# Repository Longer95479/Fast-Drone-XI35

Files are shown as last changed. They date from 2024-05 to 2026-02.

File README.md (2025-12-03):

---
layout: post
title:  "XI35 装机全过程"
date:   2024-07-15 11:40:00 +0800
tags: quadcopter drone
categories:
    - fast-drone
---

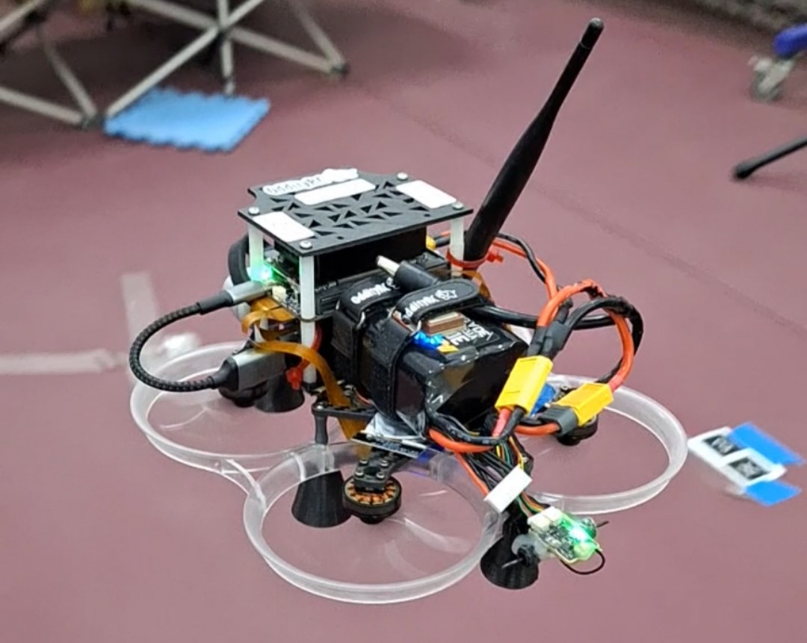
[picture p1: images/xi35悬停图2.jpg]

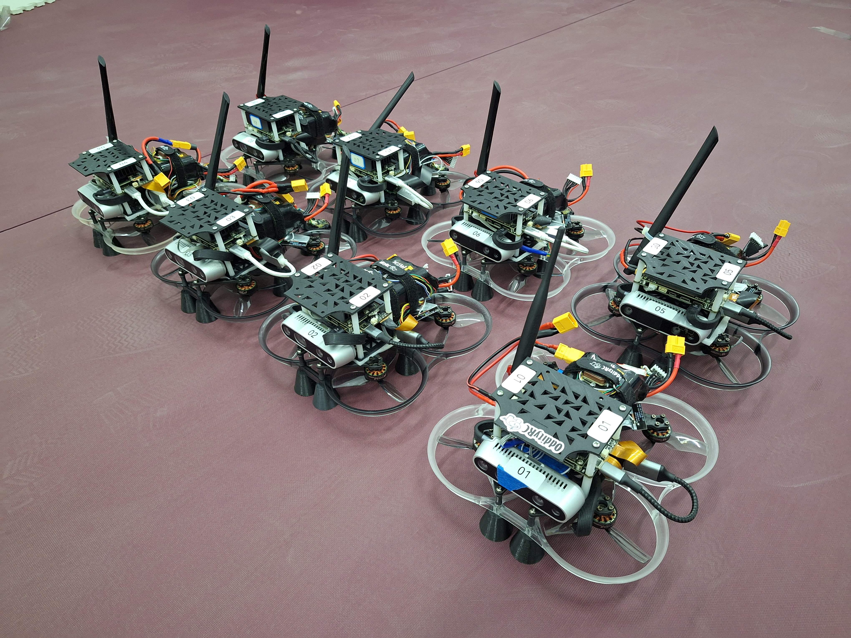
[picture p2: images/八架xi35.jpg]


本文介绍了：
- 152mm 轴距四旋翼无人机（XI35）的组装过程
- 飞控的参数配置
- 机载电脑 Jetson Orin 的系统安装与环境配置，有两种选择
  - 在宿主机上逐步地手动配置环境
  - 使用 Docker 自动配置环境
- 代码编译与启动流程
- [ ] TODO 开发流程
- 注意事项
- 开发流程

未包含的内容主要有：
- 各个模块的原理和设计逻辑
- 注意事项的具体分析

> 若需了解，可阅读本工程的其他文档，以及公开的论文。

本工程实现的功能：
- 在轴距更小的 XI35 上实现 fast-drone-250 的自主飞行避障功能
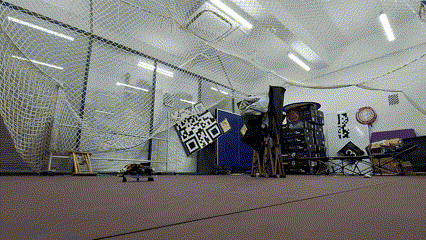
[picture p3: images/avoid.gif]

  
- 双机通信协同
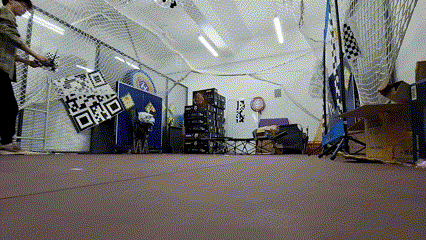
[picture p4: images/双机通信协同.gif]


- 预设航迹，搜索特定数字标识，正确识别后并降落
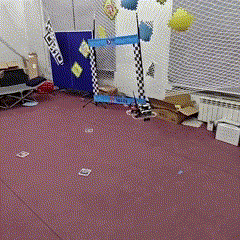
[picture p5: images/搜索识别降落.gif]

  
- 自主跟随墙面飞行
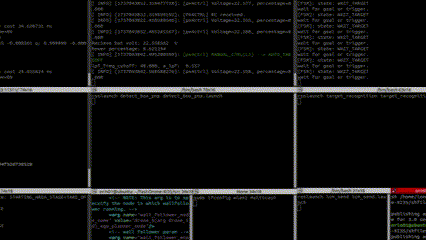
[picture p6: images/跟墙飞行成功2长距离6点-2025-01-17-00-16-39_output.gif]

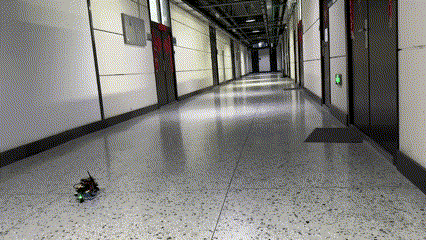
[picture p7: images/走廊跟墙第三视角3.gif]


## 目录
- [0 阅读指南](#0-阅读指南)
- [1 机体安装步骤](#1-机体安装步骤)
- [2 飞控配置](#2-飞控配置)
- [3 orin nx 配置](#3-orin-nx-配置)
- [4 docker 配置与使用](#4-docker-配置与使用)
- [5 代码编译与启动流程](#5-代码编译与启动流程)
- [6 开发流程](#6-开发流程)
- [注意事项](#注意事项)
- [参考](#参考)

## 0 阅读指南

当需要了解某个无人机部件的具体信息时：
- 所有的 `配件型号` 及 `配件的相关资料` 可在 [配件型号采购表](https://docs.qq.com/sheet/DQlVFVXBTYkpobktF?u=4ce3cf3cb1fc4960917789399c899a1a&tab=bliok2) 中找到。

从零开始组装到实现自主飞行避障：
- 可以先简单浏览第 0 - 5 章，以及 `注意事项` 和 `参考` 章节
- 简单浏览 Fast-Drone-250 的文本教程 和 视频教程
- 之后按 0-5 章的顺序安装和配置
- 遇到问题，可查看 `注意事项` 与 `参考` 章节是否提及，配合搜索引擎查找

在现有代码上开发：
- 阅读第 6 章开发流程

## 1 机体安装步骤

### 1.1 整体流程

- 将电机安装到机架上，使用四个M2*6，注意机架的上下面，孔位有凹槽的为上面

- 穿电池绑带

- 将M3转M2橡胶减震柱穿过电驱和飞控的四角安装孔（技巧：橡皮筋技巧）

- 使用M2*20安装电驱，8pin接口朝机头，接口贴着机架

- 电机线修修剪（用剥线钳），焊接(加松香)；电源线和滤波电容焊接

- 连接飞控（见下面QCG版本问题），连接电池，更改电机序号映射和转向

- 连接接收机（遥传一体模块中靠近LED的是RC接口）到飞控的 RC 端口，数传（遥传一体模块中的另一个接口）到 TELEM1 端口，GPS模块连接 到 GPS 端口

- 线穿过镂空部分把这几个模块都放到机架顶部

- ~~（略）M2\*12固定摄像头座，M2\*16固定图传天空端~~

- M3*6安装前六个铝柱的上部，<font color="#dd0000">第七个在尾部的立柱先不装</font>（b站视频说错了，应该看三维动图）

- ~~（略）M2\*12安装配重打印件~~

- 3d打印天线座安装，大的套在机架尾部，小的套在涵道圈，打印件有弹性，孔偏小，需要M3螺丝旋转	着才能穿过

- <font color="#dd0000">把各个数据线的飞控端都装上（tele2（连接到orin的），gps，接收机）</font>

- 机架，七个铝柱，涵道圈，菱形底架，从上至下叠起来后从下往上安装M3*14

- 调试完成后安装桨叶，使用M2*10安装

- 打印相机和orin的安装连接件，都是M2，立柱也是M2，配合螺母安装
    - orin载板安装孔是M3，使用M2立柱，导致只能用M2螺丝，螺帽太小会穿过，<font color="#dd0000">因此要在螺丝上加两个螺母</font>

- <font color="#dd0000">飞控上的 uart4（/dev/ttyS3） 连接到 ORIN 的 uart1（/dev/ttyTHS0）（左侧端口）</font>

参考：[NxtPX4v2开源飞控装机和配置全流程教程](https://www.bilibili.com/read/cv33197403/)

### 1.2 px4 与 orin 串口连接线的线序与焊接

由于 nxt-px4 和 orin 载板上的串口端口型号不同，需要将各自配套的线材剪断，并按照串口正确的线序进行焊接，线序对应关系如下：

|nxt-px4|黑(GND)|红(5V)|黄(Tx)|绿(Rx)|
|---|---|---|---|---|
|orin|3(GND)|x(5V)|1(Rx)|2(Tx)|

## 2 飞控配置

### 2.1 基本配置

- 测试电机转向

- 遥控器和接收机对频，并在地面站校准

- 配置通道功能，用于飞行模式切换、紧急停止等（注意：有三档的前两档一致）详见 [px4ctrl](https://gitee.com/jerry-ironman/px4ctrl)
  - 5通道2档：自稳和offboard
  - 6通道3档：是否接受命令
  - 7通道3档：急停
  - 8通道2档：px4ctrl对px4的重启

- 飞控与罗盘方向设置

- 陀螺仪与加速度计校准

- 校准地平线

细节参考 [NxtPX4v2开源飞控装机和配置全流程教程](https://www.bilibili.com/read/cv33197403/)

### 2.2 与 ORIN 通信相关的配置

主要参考 [Nxt-FC](https://github.com/HKUST-Aerial-Robotics/Nxt-FC?tab=readme-ov-file)，github 上的 readme 进行设置，<font color="#dd0000">不要按照商家给的安装教程里的进行设置</font>。主要是配置 MAV_0 的参数

- MAV_0_CONFIG: TELE2 (Serial Configuration for MAVLink (instance 0))
- MAV_0_FLOW_CTRL: Auto-detected
- MAV_0_FORWARD: Enabled
- MAV_0_MODE: External Vision
- MAV_0_RADIO_CTL: Enabled
- MAV_0_RATE: 921600 B/s

获得高分辨率和高频率的 IMU 数据所需的配置

create file in your tf-card /etc/extras.txt

```shell
mavlink stream -d /dev/ttyS3 -s ATTITUDE -r 200

mavlink stream -d /dev/ttyS3 -s HIGHRES_IMU -r 1000
```

then using the following settings:
- IMU_GYRO_RATEMAX: 2000Hz
- IMU_INTEG_RATE: 400Hz

after these settings you will have 250Hz /imu/data_raw /imu/data

## 3 ORIN NX 配置

### 3.1 安装 jetpack 5.1.3 linux for jetson orin nx modules:

- 在 PC 上的 ubuntu 里安装 sdkmanager

- 按住 REC 键并给 orin 上电，上电后可松开，之后将 typeC 插到 Recovery Port（在底板短边上的那个typec口，即 USB1），另一端连接到 PC

- 按照 sdkmanager 的引导操作即可，可选择组件安装
    - 此时 opencv 可以不装，因为此阶段安装的 opencv 不支持 cuda 加速

- 下载镜像

- 安装镜像
    - <font color="#dd0000"> 注意 username不能是大写字母，否则 sdkmanager 无法自动设置orin的用户名等后续的默认设置参数，进一步导致无法通过usb以太网连接orin </font>

    - <font color="#dd0000"> 一切安装完成后，忘记拔掉 usb 将导致板子一直无法正常启动，外接屏幕无画面，拔掉后就一切正常 </font>

- 如果 PC 上的 ubuntu 硬盘空间不足，可外接移动硬盘，将 Download Folder 和 Target HW image folder 设置在移动硬盘（FAT）里
    - <font color="#dd0000"> 注意：移动硬盘的文件系统不能是 windows 的 FAT，而应该是 EXT4，否则镜像将会安装错误 </font>

### 3.2 ROS 安装

参考 [从零制作自主空中机器人](https://github.com/ZJU-FAST-Lab/Fast-Drone-250/tree/master):

* `sudo sh -c 'echo "deb http://packages.ros.org/ros/ubuntu $(lsb_release -sc) main" > /etc/apt/sources.list.d/ros-latest.list'`

* `sudo apt-key adv --keyserver 'hkp://keyserver.ubuntu.com:80' --recv-key C1CF6E31E6BADE8868B172B4F42ED6FBAB17C654`

* `sudo apt update`

* `sudo apt install ros-noetic-desktop-full`

* `echo "source /opt/ros/noetic/setup.bash" >> ~/.bashrc`

* <font color="#dd0000">建议没有ROS基础的同学先去B站学习古月老师的ROS入门教程</font>

测试 ROS:
* 打开三个终端，分别输入
  * `roscore`
  * `rosrun turtlesim turtlesim_node`
  * `rosrun turtlesim turtle_teleop_key`

### 3.3 realsense 驱动安装

* `sudo apt-key adv --keyserver keyserver.ubuntu.com --recv-key  F6E65AC044F831AC80A06380C8B3A55A6F3EFCDE || sudo apt-key adv --keyserver hkp://keyserver.ubuntu.com:80 --recv-key  F6E65AC044F831AC80A06380C8B3A55A6F3EFCDE`

* `sudo add-apt-repository "deb https://librealsense.intel.com/Debian/apt-repo $(lsb_release -cs) main" -u`

* `sudo apt-get install librealsense2-dkms`

* `sudo apt-get install librealsense2-utils`

* `sudo apt-get install librealsense2-dev`

* `sudo apt-get install librealsense2-dbg`

* 测试：`realsense-viewer`

* <font color="#dd0000">注意测试时左上角显示的USB必须是3.x，如果是2.x，可能是USB线是2.0的，或者插在了2.0的USB口上（3.0的线和口都是蓝色的）</font>

- <font color="#dd0000">roslaunch realsense2_camera rs_camera.launch 无法正常工作，报符号错误，这是是手使用动编译的opencv4.5.4但没添加对应路径的问题 </font>
    - 解决参考 [librealsense2 camera.so: undefined symbol:ZN2cV3MatC1EV 解决笔记记录](https://blog.csdn.net/weixin_46151178/article/details/129729719)

### 3.4 安装 mavros

* `sudo apt-get install ros-noetic-mavros`
* `cd /opt/ros/noetic/lib/mavros`
* `sudo ./install_geographiclib_datasets.sh`
*  `roscd mavros`，修改 px4.launch 的串口波特率（921600）和串口名字（ttyTHS0）

### 3.5 安装ceres与glog与ddyanmic-reconfigure

* 解压`3rd_party.zip`压缩包

* 进入glog文件夹打开终端

* `sudo chmod 777 autogen.sh && sudo chmod 777 configure`

* `./autogen.sh && ./configure && make && sudo make install`

* `sudo apt-get install liblapack-dev libsuitesparse-dev libcxsparse3.1.2 libgflags-dev libgoogle-glog-dev libgtest-dev`

* 进入ceres文件夹打开终端

* `mkdir build`

* `cd build`

* `cmake ..`

* `sudo make -j4`

* `sudo make install`

* `sudo apt-get install ros-noetic-ddynamic-reconfigure`

<font color="#dd0000"> 注意，安装的版本是 `ceres 2.0.0` 版本，编译需使用 `std=c++14` 及以上，后续需把 vinsfusiongpu 里的所有包都改成 c++14 标准 </font>

### 3.6 OpenCV 安装

如果我们在 sdkmanager 中勾选了安装 opencv 的选项，安装的版本将会是 `OpenCV 4.5.4`，但不支持 cuda 加速，此时我们下载相同版本的 opencv 源码，在 CMAKE 选项上打开支持 cuda 加速的选项，再进行编译。

安装过程参考 [Jetson Orin NX 开发指南（5）: 安装 OpenCV 4.6.0 并配置 CUDA 以支持 GPU 加速](https://blog.csdn.net/qq_44998513/article/details/133778446)，注意版本的不同即可，我们安装的是 4.5.4
* install 的目录为 /usr/local/opencv-4.5.4，方便其他包的查找

<font color="#dd0000">注意，编译支持cuda的 opencv时，cmake选项里 CUDA_ARCH_BIN=8.7，而不是 7.2 </font>

### 3.7 安装 cv_bridge 功能包

为什么需要自己下载 cv_bridge 源码并编译呢？

安装 noetic full版本时已经下载了 cv_bridge 的二进制文件，其编译时使用的是 opencv 4.2 的函数，因此链接时需要链接到opencv 4.2的 so 文件，但 orin 上新安装的支持 cuda 加速的 opencv 是 4.5.4 版本，因此该 cv_bridge 只能链接到 4.5 版本的 opencv 库，vins 在执行到 cv_bridge 相关的函数时就无法正常执行，最后报内存溢出的错。

解决办法：下载 cv_bridge 的源码，然后指定 4.5 版本的opencv进行编译，编译完成后将其路径添加到 ~/.bashrc 文件中，并刷新环境变量，具体参考 [Jetson Orin NX 开发指南（5）: 安装 OpenCV 4.6.0 并配置 CUDA 以支持 GPU 加速](https://blog.csdn.net/qq_44998513/article/details/133778446)

或者是将 cv_bridge_454 的包放入同一个工作空间，其他包在 CMakeList.txt 和 package.xml 里指明依赖，一同编译即可，这是目前的做法

### 3.8 下载并编译 Fast-drone-XI35

原本需要分成两部：

- clone 浙大官方的 Fast-drone-250 的仓库
- 将其中的 vins-fusion 替换成 fins-fusion-gpu 版本

为了简化操作：
- [x] 把替换成 gpu 版本的 fast-drone-250 push 到 [Fast-Drone-XI35](https://github.com/Longer95479/Fast-Drone-XI35)，**直接 clone 该仓库即可，之后进行编译**。

其中所作的修改均是针对的 vins-fusion-gpu，包括：

- 由于 ceres 2.0.0 需使用 std=c++14，因此把 vinsfusiongpu 里的所有包的 CMakeLists.txt 都改成 c++14 标准

- 设置 OpenCV 路径为带有 GPU 加速的 opencv 4.5.4，opencv 可以指定到 `编译的文件夹` 或 `安装的文件夹`

- 由于 vins-fusion-gpu 原仓库使用的是 opencv 3，而现在安装的是 opencv 4，OpenCV 4 系列和 OpenCV 3 系列有一些变量的名称发生了改变，因此我们这里只要将相应的变量名称进行修正，就能顺利通过编译

- 具体参考：[Jetson Orin NX 开发指南（6）: VINS-Fusion-gpu 的编译和运行](https://blog.csdn.net/qq_44998513/article/details/133780129)

### 3.9 网络配置

- 使用 `iw list` 查询网卡是否支持Ad-Hoc模式，如果Supported interface modes中出现IBSS，则说明网卡支持Ad-Hoc模式

- 使用 `ifconfig` 查询想要配置成Ad-Hoc模式网卡的名称

- 使用Network Manager配置网卡，ifname为待配置的网卡名称，con-name为配置文件名称，ssid为网络名称，wifi.band为频段，wifi.channel为信道
```shell
sudo nmcli connection add type wifi ifname wlan1 con-name HITADHOC mode adhoc ssid HITADHOC wifi.band bg wifi.channel 3
```

- 通过con-name修改网络配置，ipv4.addresses为IPv4地址
```shell
sudo nmcli connection modify HITADHOC ipv4.method manual ipv4.addresses 10.10.10.11/24
```

- 通过con-name激活网络配置，激活后会开机自启动
```shell
sudo nmcli connection up HITADHOC
```

- 如果后续要删除配置，可以通过con-name删除
```shell
sudo nmcli connection delete HITADHOC
```

- LCM 安装
```shell
git clone https://github.com/lcm-proj/lcm && \
cd lcm && \
git checkout tags/v1.4.0 && \
mkdir build && cd build && \
cmake -DCMAKE_BUILD_TYPE=Release -DBUILD_TESTING=OFF -DBUILD_EXAMPLES=OFF -DBUILD_BENCHMARKS=OFF .. && \
make -j${USE_PROC} && make install
```

- LCM通信配置
```shell
sudo ifconfig wlan1 multicast
sudo route add -net 224.0.0.0 netmask 240.0.0.0 dev wlan1
```

### 3.10 安装 onnxruntime

```shell
pip install onnxruntime
```

### 3.11 安装 skimage
```shell
pip install scikit-image
```

## 4 Docker 配置与使用
底层基础镜像：NVIDIA L4T JetPack r35.3.1
官方镜像地址：https://catalog.ngc.nvidia.com/orgs/nvidia/containers/l4t-jetpack
### 4.1 构建基础环境镜像Dockerfile.jetson_base
基础环境镜像包含了运行Fast-Drone-XI35所需要的各种软件库。
- ros-noetic-base及其部分功能包
- OpenCV4.5.4-cuda版本
- cv_bridge4.5.4，适配的opencv4.5.4，已添加进ros环境，功能包名称cv_bridge_454
- realsense2驱动库
- mavros功能包
- glog-0.5
- ceres-2.0.0
- lcm

部分软件库（ceres、glog和cv_bridge）和编译一些软件库所需要的额外的文件（比如编译opencv_contrib需要一些额外文件）打包进一个压缩包3rd_party.zip，放在docker执行的上下文目录，供构建镜像时解压使用。
构建环境基础镜像，在终端执行：
```shell
make jetson_base
```

**具体使用见 4.6**

### 4.2 构建Fast-Drone-XI35工程镜像Dockerfile.jetson
在Dockerfile.jetson_base的基础上构建，从github上拉取最新的Fast-Drone-XI35并进行编译，加入容器初始化脚本。
由于dockerhub在国内无法访问，基础环境镜像暂时没有push到远程仓库，通过docker save打包成.tar文件，借助u盘拷贝至宿主机，再通过docker load解压得到基础环境镜像local/fastdronexi35:orin_base_35.3.1。
要构建Fast-Drone-XI35镜像，在终端执行:
```shell
make jetson
```
初始化脚本"container_init.sh"说明：
初始化脚本也放在构建镜像的上下文目录，构建阶段拷贝至镜像/root目录下，用于执行启动容器时的一些初始化操作，目前的初始化操作比较简单，主要是启动ssh服务，还有一个操作是改变mavros的px4.launch中的参数用于设配实际硬件，这样避免了重新构建基础镜像。
### 4.3 容器启动脚本说明
容器启动脚本“container_run.sh”用于对Fast-Drone-XI35工程镜像执行docker run操作，并实现必要的自定义配置，后续可根据需求进行修改，下面对目前容器启动配置进行详细介绍。
```shell
docker run -itd --privileged=true --network host \
        --mount type=bind,source=${HOME}/Docker_Data,target=/root/data \
        --mount type=bind,source=/dev,target=/dev \
        --mount source=Fast-Drone-XI35,target=/root/Fast-Drone-XI35 \
        --runtime=nvidia --gpus all \
        --name fd_runtime \
        fastdronexi35:orin /bin/bash
```
- 通过“--privileged=true”赋予容器对宿主机全面的访问权限，再通过“--mount type=bind,source=/dev,target=/dev”挂载宿主机的/dev实现容器对宿主机设备资源的无障碍访问。
- “--network host”配置容器的网络模式为host主机模式，容器和宿主机共享ip和端口号，相比于需要进行端口映射bridge模式，host模式下更方便远程主机与容器实现双向通信，比如ros多机的场景。但要注意与宿主机端口冲突的问题。
- “--mount type=bind,source=${HOME}/Docker_Data,target=/root/data”通过bind mounts将宿主机指定目录挂载至容器内。宿主机目录需要提前建立，并且宿主机目录不管是否为空都会覆盖容器目录（相当于在容器内创建了指向宿主机目录的软连接），主要用于共享宿主机数据以及永久性存储容器的数据。
- “--mount source=Fast-Drone-XI35,target=/root/Fast-Drone-XI35”通过数据卷（volumes）挂载方式，实现Fast-Drone-XI35工程目录在宿主机和容器之间的双向互通，此操作会在宿主机docker目录下创建数据卷，并在启动容器时将容器内的Fast-Drone-XI35挂载到数据卷，类似于软连接，在数据卷中的修改会同步到容器，从而便于在宿主机直接修改代码。注意启动容器时若数据卷不为空，则数据卷会覆盖容器目录。
- “--runtime=nvidia  --gpus all”使容器能访问gpu，前提是已经装好NVIDIA Container Toolkit，官方安装教程：https://docs.nvidia.com/datacenter/cloud-native/container-toolkit/latest/install-guide.html
### 4.4 VSCode SSH配置
通过vscode的Remote SSH插件远程连接至宿主机，在资源管理器打开挂载Fast-Drone-XI的数据卷，即可实现代码开发（前提是容器内Fast-Drone-XI正确挂载到宿主机数据卷）。实现步骤如下：
- 安装remote-ssh插件

<p align="center">
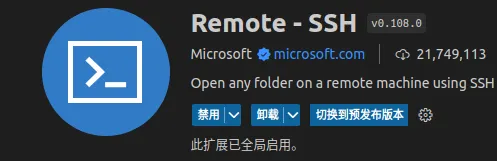
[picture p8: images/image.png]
  
</p>

- 点击左侧的远程资源管理器，点击“+”新建远程，输入宿主机的用户名和ip，由于访问docker的数据卷需要root权限，所以需要以root身份登录，即用户名为root。

<p align="center">
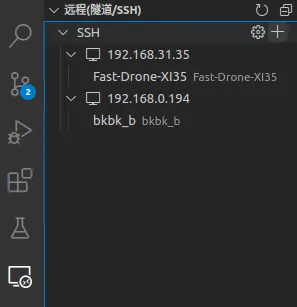
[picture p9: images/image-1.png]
  
</p>

如果无法登录，检查宿主机的root密码是否正确，一般情况下ubuntu的root没有初始密码，这种情况下无法以root登录的，需要通过“sudo passwd root”重新设置root密码。

- 登录成功后即可编辑代码，并且修改会同步至容器。

<p align="center">
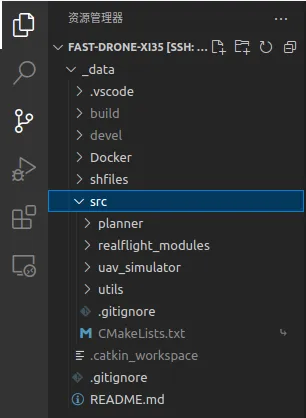
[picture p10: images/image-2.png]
  
</p>

### 4.5 Fast-Drone-XI35远程同步更新
需求场景：github远程仓库有更新，需要更新容器内的Fast-Drone-XI35。
目前有两种更新方式，宿主机更新和工程镜像更新。
- 宿主机更新：
容器内Fast-Drone-XI35已挂载到宿主机的docker数据卷，对数据卷的任何操作都会同步到容器内，因此可以对宿主机的Fast-Drone-XI35数据卷使用git pull更新工程。这种更新方式效率高，但是更新发生在宿主机数据卷，没有更新镜像，若要形成新的镜像，需要对容器进行commit。
- 工程镜像更新：
重新构建工程镜像，构建时会拉取远程仓库最新的版本，最后生成带有Fast-Drone-XI35最新版本的镜像。主要流程如下：
①停止并删除正在运行的容器（fd_runtime）
②删除工程镜像（fastdronexi35:orin）
③删除宿主机Fast-Drone-XI35数据卷
④运行make jetson构建新的工程镜像
上述操作已集成在"update_jetson.sh"脚本中，当需要进行镜像更新时，直接运行该脚本即可，注意需要宿主机有基础环境镜像（tag为"local/fastdronexi35:orin_base_35.3.1"），否则无法构建。
### 4.6 容器部署简要流程

首先 clone 本仓库，之后的从构建基础环境镜像到运行容器的整个流程，所有命令在/Docker/Dockerfile目录下执行。

```shell
git clone https://github.com/Longer95479/Fast-Drone-XI35.git
```

- 构建基础环境镜像: local/fastdronexi35:orin_base_35.3.1
```shell
make jetson_base
docker tag fastdronexi35:orin_base_35.3.1 local/fastdronexi35:orin_base_35.3.1
```
或者 直接从移动硬盘里加载镜像的 tar 文件
```shell
sudo docker load -i fastdronexi35_base.tar
```

- 在本工程的 `/Docker/Dockerfile`下执行命令，构建工程镜像: fastdronexi35:orin
```shell
make jetson
```
- 首次编译完成后，执行容器启动脚本
```shell
./container_run.sh
```

后续重启后，只需执行以下命令启动容器
```shell
sudo docker start fd_runtime
```

- 进入容器的 bash

```shell
sudo docker exec -it  fd_runtime bash
```

- 如果需要更新工程镜像，则执行
```shell
./update_jetson.sh
```

## 5 代码编译与启动流程

### 5.1 前置准备

**1.使用网卡局域网连接无人机**

配置网卡
- 使用Network Manager配置网卡，ifname为待配置的网卡名称，con-name为配置文件名称，ssid为网络名称，wifi.band为频段，wifi.channel为信道(只需更改wlan1为无线网卡)

  ```sudo nmcli connection add type wifi ifname wlan1 con-name HITADHOC mode adhoc ssid HITADHOC wifi.band bg wifi.channel 3```

- 通过con-name修改网络配置，ipv4.addresses为IPv4地址(10.10.10.11中末位的11-19是无人机用的ip，不要重复设置)

  ```sudo nmcli connection modify HITADHOC ipv4.method manual ipv4.addresses 10.10.10.11/24```

- 通过con-name激活网络配置，激活后会开机自启动

  ```sudo nmcli connection up HITADHOC```

- 如果后续要删除配置，可以通过con-name删除

  ```sudo nmcli connection delete HITADHOC```

- 查看已配置的网络连接

  ```sudo nmcli con show```

- 连接无人机

  ```ssh orin04@10.10.10.14```

**2.获取ip地址后使用路由器连接**

- 使用nmcli命令配置wifi连接

  ```sudo nmcli device wifi```

- 查询wifi列表

  ```sudo nmcli device wifi list```

- 更改连接wifi(查找不到wifi时重新扫描)

  ```sudo nmcli device wifi connect Drone_WiFi password buzhidao```

- 查看ip

  ```ifconfig```

- 使用局域网连接

  ```sh orin04@192.168.3.101```

**3.使用terminator连接**

- 查看隐藏文件和文件夹

  ```ls -a```

- 查找terminator配置文件(.config/terminator目录下)

  ```cd ~/.config/terminator```

- 查看当前目录下文件的详细信息，terminator中仅有config文件发挥作用，所以重只需查看config的软路由

  ```ll```

- 默认使用网卡连接，如果需要更改为wifi连接，可以替换原有配置中的本地ip后更改路由

- vim 内的批量替换命令

  ```:%s/10.10.10.11/192.168.3.100/g```

- 更改软路由

  ```sudo ln -sf config-orin01-nodocker config```

- 打开无人机控制系统

  ```terminator -l drone_1```

### 5.2 运行无人机的不同功能

- ssh 连接到 orin 板，如 `ssh orin01@10.10.10.11`

悬停功能：

- 启动里程计
  - `sh Fast-Drone-XI35/shfiles/rspx4.sh`

- 启动运动控制器
  - `roslaunch px4ctrl run_ctrl.launch`

可选功能：

- 启动 ego-planner
  - `roslaunch ego_planner single_run_in_exp.launch`

- 打开下视摄像头，并进行数字标识检测、定位、识别
  - `roslaunch jetson_csi_cam jetson_csi_cam.launch sensor_id:=0`
  - `roslaunch detect_box_pnp detect_box_pnp.launch`
  -  `roslaunch target_recognition target_recognition.launch`

- 打开多机协同搜索的状态机，以及目标结果融合
  - `roslaunch search_plan search_plan.launch`
  - `roslaunch target_merge target_merge.launch`

- 打开多机自组网通信
    - `sudo ifconfig wlan1 multicast`
    - `sudo route add -net 224.0.0.0 netmask 240.0.0.0 dev wlan1`
    - `roslaunch lcm_receive lcm_receive.launch`
    - `roslaunch lcm_send lcm_send.launch`

起飞：

- `sh Fast-Drone-XI35/shfiles/takeoff.sh`

### 5.3 调参

一些常用的参数可能需要频繁调整，但参数分布在不同文件里，为了提高修改效率，编写了脚本批量修改参数，无需直接在原文件内修改，只需在 `Fast-Drone-XI35/config_scipt` 目录下修改 `xxx.yaml` 配置文件，文件里已列出一系列参数和值。修改完毕后可执行脚本 读取 和 真正写入 参数：

```
python3 read_global_config.py global_config_indoor.yaml
python3 set_global_config.py global_config_indoor.yaml
```

如需了解有哪些参数需要配置，请阅读 `config_scipt/global_config_indoor.yaml` 文件。大致可分为两类：
- 机间特异性配置
- 与飞行场地大小相关的参数配置

pid 的参数需单独在 `Fast-Drone-XI35/src/realflight_modules/px4ctrl/config` 文件内修改。

## 6 开发流程
### 曲线日志的使用与解析
在开发过程中，难免有时需要对一个变量随时间的变化情况进行观察，或者对自己打印的某个log在实验结束后进行复盘，基于此开发了如下功能：

- 将ROS自带的文件系统日志记录到代码主目录下的/log文件夹

- 通过在代码中调用ROS日志输出特定格式的键值对来记录“曲线日志”

- 使用/scripts/process_log.py对所有架次的日志进行解析，输出为文本日志和csv曲线日志

下面是具体开发指南：

1. 修改ROS日志在文件系统内的默认位置

ROS的日志在启动时会获取ROS_LOG_DIR环境变量的值，将日志保存在此位置，所以需要在.bashrc添加一个环境变量。

- 在非Docker环境中，需要在~/.bashrc中自行添加环境变量（下面的绝对路径换成自己的代码中log目录位置）。

```
export ROS_LOG_DIR=/home/zhangrun/code/Fast-Drone-XI35/log
```

- 在Docker环境中，配置脚本已经添加了加入环境变量的步骤，所以无需操作。

2. 在代码中记录曲线日志

通过键值对[status]:[12.76]的格式调用ROS_INFO或ROS_WARN或ROS_INFO_THROTTLE等进行记录，如：

```
ROS_INFO("[odom_tx]:[%f] [odom_ty]:[%f] [odom_tz]:[%f], tmp_T.x(), tmp_T.y(), tmp_T.z());
```

注意只支持英文字母。

3. 日志解析

通过在代码/scripts/process_log.py脚本进行解析处理

```
python3 scripts/process_log.py
```

将会有如下输出：

```
Processing /home/zhangrun/code/Fast-Drone-XI35/scripts/../log/2d61da22-a4b5-11f0-b4af-488f4b616bfc ...
Done: /home/zhangrun/code/Fast-Drone-XI35/scripts/../log/2025-10-09 10:10:50
Processing /home/zhangrun/code/Fast-Drone-XI35/scripts/../log/711678c8-a4b4-11f0-9342-488f4b616bfc ...
Done: /home/zhangrun/code/Fast-Drone-XI35/scripts/../log/2025-10-09 10:05:34
```

上边参考输出表示将2d61da22-a4b5-11f0-b4af-488f4b616bfc文件夹的日志输出到log/2025-10-09 10:10:50目录下，其中有两种日志：'2025-10-09 10:10:50.csv'  '2025-10-09 10:10:50.log'，分别对应曲线日志和文本日志。

4. 曲线日志的查看

通过ROS的Plotjuggler进行查看.csv格式的曲线日志。亦可以将日志下载到Windows电脑，通过win平台的Plotjuggler进行查看

安装：

```
sudo apt install ros-noetic-plotjuggler-ros
```

启动：
```
rosrun plotjuggler plotjuggler
```

导入.csv文件，选定timestamp为X轴后，将想要显示的曲线拖动到右侧表中即可显示。

<p align="center">
  <img src="images/plotjuggler-1.png" width="90%">
</p>

<p align="center">
  <img src="images/plotjuggler-2.png" width="90%">
</p>

## 注意事项

### 飞控相关

- 安装好后typeC不好插

- 小心滤波电容短路

- QGC v4.0.11无法识别 px4 pro 1.14.0
  - QGC 4.3.0 可以识别

- imu频率在地面站上看一直是50Hz，不知用NX板连接 SER_TELE2 时会不会达到250Hz
  - 会

- 智能充充电电流设置为1.3A会时不时自动停止充电，需要频繁人为重启，设置为1A则正常（电池充放电能力为0.5C，既 3000mAh*0.5h^-1 = 1500mA = 1.5A）

- 电机线焊接方向没选择好，导致挤在一起，可能会影响散热
  - ！！！加上电源线没焊好，会挡住飞控上的 TELE2 接口，不得不重新焊接

### Orin 相关

- orin载板安装孔是M3，使用M2立柱，导致只能用M2螺丝，螺帽太小会穿过，因此要在螺丝上加两个螺母

- orin和nxtpx4通过串口相连，但两端的接口不同，需要自己焊接线

- px4的/dev/ttyS3 连接到 orin 的 /dev/ttyTHS0

- 安装ceres与glog与ddyanmic-reconfigure时，执行 ./autogen.sh && ./configure && make && sudo make install 前要加两句 sudo chmod 777 autogen.sh && sudo chmod 777 configure

- unable to locate package libcxsparse3.1.2
    - 使用sdkmanager预装的opencv不支持cuda，需要卸载，重新安装支持cuda加速的版本
    - 或者不卸载，直接安装支持 cuda 加速的版本，之后cmake文件里把路径指向编译所在的文件夹，因为卸载时用 autoremove会把 ros的full版本删掉一部分，需要重新下回来，并照着vinsfusiongpu的readme修改路径
    - 更好的操作是不要使用 sudo make uninstall 卸载 opencv，而是
        - 找到之前装opencv的build文件夹，进入后执行卸载指令 `sudo make uninstall`
        - 然后再把之前留在usr文件夹里的剩余文件都删掉
        - `sudo rm -r /usr/local/include/opencv4  /usr/local/share/opencv4 /usr/local/lib/libopencv* `
        - `sudo rm -r /usr/include/opencv4  /usr/share/opencv4 /usr/lib/libopencv* `
`

- roslaunch realsense2_camera rs_camera.launch 无法正常工作，报符号错误，这是是手使用动编译的opencv4.5.4但没添加对应路径的问题
    - 解决参考 [librealsense2 camera.so: undefined symbol:ZN2cV3MatC1EV 解决笔记记录](https://blog.csdn.net/weixin_46151178/article/details/129729719)

- VINS无法正常运行，原因有多个
  - 一个是是编译支持cuda的 opencv时， cmake选项里 CUDA_ARCH_BIN=8.7，填成了7.2
  - 另一个重要原因是，安装 noetic full版本时已经下载了 cv_bridge 的二进制文件，其编译时使用的是 opencv 4.2的函数，因此链接时需要链接到opencv 4.2的 so文件，但orin上新安装的支持cuda加速的opencv是 4.5.4 版本，因此该cv_bridge 只能链接到 4.5 版本的opencv库，vins在执行到cv_bridge 相关的函数时就无法正常执行，最后报内存溢出的错。解决办法：下载 cv_bridge 的源码，然后指定 4.5版本的opencv进行编译，编译完成后将其路径添加到 ~/.bashrc 文件中，并刷新环境变量
  - 参考 [Jetson Orin NX 开发指南（6）: VINS-Fusion-gpu 的编译和运行_jetson orin nx跑vins-CSDN博客](https://blog.csdn.net/qq_44998513/article/details/133780129)

- 设置好外参初始值后，里程计输出出现姿态较准确，但平移量反复波折，仿佛被约束在一点，不随实际运动而运动，且容易出现巨大漂移
  - 外参中旋转矩阵的符号错了，本来以为相机坐标系是z朝前y朝上，实际情况时z朝前y朝下，修改后里程计正常

- 自动起飞后会超调一下

- 飞行过程上下起伏，可能需要调一下PID参数

- 起飞和飞行时机身倾斜，需要校准一下地平线

- LCM节点启动后报错：Error while loading shared libraries: liblcm.so.1: cannot open shared object file: No such file or directory
    - [$ sudo ldconfig -v](https://github.com/CogChameleon/ChromaTag/issues/2)

### 调试相关

- 需要先生成公钥，然后执行该命令，之后便不需要再输入密码即可连接

  ```ssh-copy-id orin01@10.10.10.11```

- 命令行连接wifi

```shell
sudo nmcli device wifi list
sudo nmcli device wifi connect Drone_WiFi password buzhidao
```

- vim 内的批量替换命令

  ```%s/10.10.10.11/192.168.3.100/g```

- 更改软路由

  ```sudo ln -sf config-orin01-nodocker config```

- 常用参数修改，如起飞高度

```shell
/home/orin01/Fast-Drone-XI35/config_scipt
python3 read_global_config.py global_config_indoor.yaml
python3 set_global_config.py global_config_indoor.yaml
```

- pid调参

  ```/home/orin01/Fast-Drone-XI35/src/realflight_modules/px4ctrl/config```

- 打开无人机控制系统

  ```terminator -l drone_1```

## 参考

- [OddityRC XI35pro Assembly Guide](https://oddityrc.com/blogs/assembly-guides/xi35pro-frame-assembly-guide)

- [OmniNxt](https://hkust-aerial-robotics.github.io/OmniNxt/)

- [怪象XI35装机视频_哔哩哔哩_bilibili](https://www.bilibili.com/video/BV1Au411t7tV/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)

- [3.5寸圈圈机怪象XI35装机教程_哔哩哔哩_bilibili](https://www.bilibili.com/video/BV1QG411E7NQ/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)

- [NxtPX4v2开源飞控装机和配置全流程教程](https://www.bilibili.com/read/cv33197403/)

- [Jetson Orin NX 开发指南（5）: 安装 OpenCV 4.6.0 并配置 CUDA 以支持 GPU 加速](https://blog.csdn.net/qq_44998513/article/details/133778446)

- [Jetson Orin NX 开发指南（6）: VINS-Fusion-gpu 的编译和运行_jetson orin nx跑vins-CSDN博客](https://blog.csdn.net/qq_44998513/article/details/133780129)

- [Fast-Drone-250](https://github.com/ZJU-FAST-Lab/Fast-Drone-250)

- [wall-follower-fastdrone-250](https://github.com/Longer95479/wall-follower-fastdrone-250/)

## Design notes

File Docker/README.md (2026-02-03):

# Docker 使用

## nvidia jetson平台

1. 构建基础镜像

```bash
make jetson_base
```

2. 构建工程镜像

```bash
make jetson
```

3. 容器启动

```bash
### 首次容器启动
./container_run.sh
### 后续容器启动
docker start fd_runtime
docker exec -it  fd_runtime bash
```

## x86 平台

⚠️ 前置要求

1. 宿主机必须正确安装好Nvidia驱动，使用nvidia-smi测试输出，CUDA Version字段必须大于等于11.8

2. 宿主机必须正确安装好Nvidia Docker Toolkit
```bash
curl -fsSL https://nvidia.github.io/libnvidia-container/gpgkey | sudo gpg --dearmor -o /usr/share/keyrings/nvidia-container-toolkit-keyring.gpg \
  && curl -s -L https://nvidia.github.io/libnvidia-container/stable/deb/nvidia-container-toolkit.list | \
    sed 's#deb https://#deb [signed-by=/usr/share/keyrings/nvidia-container-toolkit-keyring.gpg] https://#g' | \
    sudo tee /etc/apt/sources.list.d/nvidia-container-toolkit.list

sudo apt-get update
sudo apt-get install -y nvidia-container-toolkit
sudo nvidia-ctk runtime configure --runtime=docker
sudo systemctl restart docker
```

3. 确认电脑的CUDA_ARCH_BIN，对Dockerfile.pc的ARG CUDA_ARCH_BIN=7.5（默认）进行修改

```bash
git clone https://github.com/NVIDIA-AI-IOT/deepstream_tlt_apps.git
cd deepstream_tlt_apps/TRT-OSS/x86
nvcc deviceQuery.cpp -o deviceQuery
./deviceQuery
### 输出
Detected 1 CUDA Capable device(s)

Device 0: "NVIDIA GeForce GTX 1660 SUPER"
  CUDA Driver Version / Runtime Version          12.2 / 11.8
  CUDA Capability Major/Minor version number:    7.5

CUDA Capability Major/Minor version number这个字段的数字就是CUDA_ARCH_BIN
###
```

4. 由于需要从docker Hub pull一个base镜像，需要提前解决docker的代理问题，否则会出错

参考：

```bash
vim /etc/docker/daemon.json
###
# 添加以下内容
{
 "registry-mirrors": ["https://docker.1ms.run", "https://docker.1panel.live/"]
}
###
sudo systemctl daemon-reload
sudo systemctl restart docker
```

1. 下载TensorRT到Docker文件夹下

下载地址（需要登录）：
https://developer.nvidia.com/downloads/compute/machine-learning/tensorrt/secure/8.6.1/tars/TensorRT-8.6.1.6.Linux.x86_64-gnu.cuda-11.8.tar.gz

2. 构建Docker镜像

```bash
cd Docker/Dockerfile
make pc
```

中间会提示

- ⚠️ Please download TensorRT and put it in the parent directory (../) url:https://developer.nvidia.com/downloads/compute/machine-learning/tensorrt/secure/8.6.1/tars/TensorRT-8.6.1.6.Linux.x86_64-gnu.cuda-11.8.tar.gz
Press any key to continue...
安装第一步下载好tensorRT文件到指定位置，此处可按任意键跳过

- Do you want to use a proxy? [y/n]
是否使用代理进行接下来的构建，由于github、国外软件源的存在，不使用代理会有几率存在网络问题，推荐使用代理，回车默认y

- Use default proxy (http://127.0.0.1:7897) (http://127.0.0.1:7897)?
默认代理地址指向本机代理软件的地址和端口，如果想要更改代理地址，输入n后进行修改。 ⚠️ 注意修改代理地址时，一般HTTP_PROXY和HTTPS_PROXY都是http开头的代理地址

构建完成后

```bash
docker image ls
```

输出

```bash
REPOSITORY      TAG IMAGE ID        CREATED         SIZE
fastdronexi35   pc  a615436b212d    19 hours ago    24.4GB
```

3. 实例化Docker容器

其中$TARGET_DIR需要替换为宿主机的代码目录，或者其他的想要映射到容器内的目录

- -v $TARGET_DIR:/root/Fast-Drone-XI35 作用是将宿主机的$TARGET_DIR目录映射到容器内的/root/Fast-Drone-XI35，实现宿主机和容器共同使用同一份文件。两个系统均可对文件进行修改。

```bash
xhost +local:root # 允许本地 root 显示 X 窗口

docker run -it \
--name fd_runtime_pc \
--gpus all \
--net=host \
--privileged \
-e DISPLAY=$DISPLAY \
-e QT_X11_NO_MITSHM=1 \
-v /tmp/.X11-unix:/tmp/.X11-unix:rw \
-v $TARGET_DIR:/root/Fast-Drone-XI35 \
fastdronexi35:pc \
bash
```

4. 测试容器

- 进入容器终端

```bash
docker exec -it fd_runtime_pc bash
```

- 建议将代码source setup.bash放入.bashrc环境变量中,同时配置ROS_LOG_DIR的环境变量，根据自己实际的容器中代码路径下述命令

```bash
echo 'export ROS_LOG_DIR=/root/Fast-Drone-XI35/log' >> /root/.bashrc
echo "source /root/Fast-Drone-XI35/devel/setup.bash" >> /root/.bashrc
```

- 运行VINS-Fusion测试

```bash
# 在代码根目录进行编译
catkin_make -DCMAKE_EXPORT_COMPILE_COMMANDS=ON -DCMAKE_BUILD_TYPE=Release
# source环境变量(如果已经添加过环境变量，则跳过)
source devel/setup.bash 
# 启动各个节点
roslaunch imu_filter imu_filter.launch
roslaunch superpoint superpoint_frontend.launch
roslaunch vins fast_drone_250.launch
roslaunch vins rviz.launch
# 播放数据集
rosbag play your_dataset.bag
```

⚠️ 注意第一次运行前端superpoint_frontend.launch会卡住，是正常现象，内部在进行跨平台的.onnx文件构建，等待3~4分钟即可正常运行，下一次也可正常启动。

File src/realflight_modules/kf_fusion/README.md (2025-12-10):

# 功能
实现了基于ESKF的松耦合定位框架kf-fusion，通过松耦合的形式融合IMU、GNSS、外部里程计（VINS）和动捕，输出平滑、高频的定位信息（位置、姿态和速度）。
1. 通用IMU-ESKF框架，不考虑地球自转带来的非惯性系虚拟力，适用于低成本IMU。
2. 支持以松耦合的形式融合外部里程计/动捕、GNSS（后续支持），融合里程计或动捕时支持动态标定外参（杆臂）。
3. 实现了基于IMU预积分的延迟更新，相比于传统延迟更新方式更高效、平滑。

# 使用
1. 配置位于/config目录下的config.yaml参数文件，关键配置信息包括：IMU话题名、里程计/动捕话题名、是否使用动捕、里程计/动捕机体系到IMU系的外参。
2. 运行kf_fusion：
``` plain
roslaunch kf_fusion kf_fusion.launch
```
3. 若需可视化，运行：
``` plain
roslaunch kf_fusion rviz.launch
```
4. 注意，运行kf_fusion后，需静止等待5s左右完成初始化，控制台输出初始化信息后才能运动。

# 代码框架说明
以下介绍程序的关键模块，包括状态管理、初始化、ESKF框架以及系统Pipeline，请需要进行二次开发的同学仔细阅读。
## 状态管理
对每类状态单独定义一个没有继承关系的类，并使用variant对所有状态进行包装实现类型擦除，用一个map存储所有系统状态，使用variant的主要目的是避免使用基于多态的类型擦除，因为这种方法会频繁使用开销较大的dynamic_cast作下行转换，效率较低。  
最底层的状态类（一级状态类）是按照状态的数据定义和更新方式区分的，目前主要有两个状态基类，分别是OriBase（旋转）和VecBase（三维向量），状态基类记录该状态的localSize（对应误差状态的维数），OriBase维护的基本数据格式是Sophus::SO3d，更新方式为右扰动，VecBase的基本数据格式是Vector3d。  
IMU状态以及外参状态（统称为二级状态类）继承自这些状态基类，其中IMU姿态状态继承自OriBase，外参旋转状态继承自VecBase，其余继承自VecBase，二级状态类需要指定状态类型StateType（枚举值）以及排列序号。  
三级状态是利用variant封装的状态类SystemState，也是最终插入到状态池（map）的状态类型。定义用于生成SystemState的模板类，在该类中实现通用的二级状态访问操作（基于visitor）以及工厂函数。
### StateBase以及二级状态类
**重要成员变量**：  
*LocalDim*：局部维度或误差状态维度，在一级状态中定义，编译常量。  
*state_value*: 状态数值（SO3或Vector），在一级状态中定义。  
*is_constant*：是否是常量状态（涉及到是否会在kf过程中对其进行更新），在一级状态中定义。  
*start_index*：在总状态向量中的索引，在一级状态中定义，编译时确定，运行时赋值。  
*Order*：状态排列序号，在二级状态中定义，编译常量。  
**重要成员方法**：  
*update()*：输入后验误差状态，对状态进行更新。  
*localSize() / startIndex()*：返回对应成员变量的数值。  

### SystemState/DefineVariantState类
模板类，基于std::variant包装二级状态，定义了一系列编译时确定的常量成员方法，用于实现快捷简便的系统状态增删。  
**重要成员方法：**  
*orderIndex() / localSize() / update()* 等：基于visitor模式访问枚举体内部二级状态的成员变量或方法。  
*viewAs() / viewConstAs()* ：模板函数，模板参数为二级状态类型，通过std::get方法返回二级状态引用。  
*create()* : 工厂函数，传入状态初始值的地址和二级状态类型的枚举，返回创建好的三级状态SystemState。  
*sumOfLocalSize()*：编译常量成员方法，返回总的状态维数（各状态的local size之和）。  

### StateManager类
**重要成员变量：**  
*state_pool*：map类，系统状态池，键为每个状态的uid，值为variant包装的三级状态类。  
**重要成员方法：**  
*insertState()*：在系统初始化时调用，输入状态uid，状态类型枚举和初始值地址，构造状态并插入到状态池中。  
*updateState()*：kf完成后调用，输入后验误差状态向量，按顺序调用各状态的更新函数进行更新。  
*getXXXState()*：返回特定状态的状态数值引用。  

### 添加新的状态流程
1. 判断该状态是否属于OriBase或VecBase，若不是则需要自定义新的状态基类，定义方式按照已有状态基类。然后定义二级状态继承自状态基类，指定状态类型和排列序号（均为编译时常量）。
2. 在commons.h中添加枚举值，包括状态类型StateType，状态排列序号StateOrder，若是需要定义新的状态基类则还需要添加该状态基类的local_dim(local size)；指定该状态的uid，在commons.h中定义内联函数getxxxStateUid()，返回该状态的uid。
3. 在SystemState模板参数中添加二级状态类。
4. 确定该状态的初始值以及初始协方差，在kf_coordinator的init函数中通过state_manager的接口向状态池中插入该状态。

## 初始化——StateInitializer类
用于初始化kf状态，主要是导航系下的位姿、速度和零偏，为了实现灵活的初始化（基于odom或基于gps），因此单独将初始化过程封装为一个类。  
**重要成员变量：**  
*state*：StateInit类型，存储了状态的初始值，包括姿态、位置、速度、零偏、初始化时刻的imu信息。  
*imu_queue*：imu缓存队列，用于初始化零偏。  
*odom_que*：里程计队列，用于初始化除零偏以外的状态。  
*is_bias_init*：bool类型，是否完成零偏初始化。  
*is_state_init*：bool类型，是否完成所有状态的初始化。  
**重要成员方法：**  
*initState()*：初始化逻辑主要执行函数，输入观测meas，返回是否初始化成功。若输入meas为imu并且没有完成零偏初始化，则调用initGyroBias()进行零偏初始化；若输入meas为里程计并且已完成零偏初始化，则调用initByOdom()完成其他状态初始化。  
*initGyroBias()*：根据固定时间窗口的imu数据初始化陀螺仪零偏。  
*initByOdom()*：接收odom的位姿和速度，根据odom时间戳以及imu缓存队列，将odom的位姿和速度积分到最新的imu时刻，积分结果作为初始位姿和速度。  

## ESKF框架——KfCoordinator类
**重要成员变量：**  
*imu_que*：维护固定时间长度的imu队列，主要用于实现延迟更新。  
*state_manager*：状态管理器，内部维护了系统状态池，kf_coordiantor通过该成员变量获取和操作系统状态信息。  
*state_cov*: 系统状态协方差矩阵，MatrixXd类型，维度取决状态数量和各状态维数。  
*imu_noise_cov*：imu测量的噪声矩阵，包含高斯白噪声和零偏随机游走噪声，由于imu的递推采用中值积分，因此该噪声矩阵维度是18。  
*obv_residual*：观测残差向量，存储VectorXd类型的vector，容器内每个元素对应一个观测信息形成的观测残差。  
*obv_jocabian*：观测雅克比矩阵，存储MatrixXd类型的vector，容器内每个元素存对应一个观测信息对应观测模型的雅克比矩阵，行数为观测残差维度，列数为系统状态维度。注意obv_residual和obv_jocabian里内的元素必须是一一对应关系。  
*obv_R*：观测的噪声矩阵。  
*is_init*：bool类型，是否完成kf的初始化。  
**重要成员方法：**  
*insertStateWithCov()*：插入非常量状态，需指定：该状态uid，状态类型枚举，状态初始值以及初始协方差。  
*insertConstState()*：插入常量状态，不需要输入协方差，默认协方差为极小值。  
*init()*：输入state_initializer的初始化结果，调用insertStateWithCov()或insertConstState()初始化系统状态。  
*imuStatePropagate()*：imu状态递推实现，根据输入的imu信息传播imu状态和协方差，递推方法为中值积分。  
*processImuMeas()*：将新的imu测量push到队列，并控制队列的长度，调用imuStatePropagate()完成imu状态递推。  
*getDelayUpdateInfo()*：输入观测信息的观测时间，返回用于延迟更新的信息（延迟更新雅克比矩阵，延迟预积分结果）。  
*addResidualJacobian()*：输入某次观测信息对应的观测残差、观测雅克比、id_size_pair以及该观测对应的延迟更新雅克比。输入的观测残差直接push到obv_residual；输入的观测雅克比是用vector存储的，每个元素对应该观测残差对某个系统状态的雅克比，通过id_size_pair指明该雅克比关联状态的start_idx和local_size，从而在addResidualJacobian()内部实现对雅克比矩阵的扩展（列扩展为系统状态总维度），最后将扩展后的观测雅克比乘以延迟更新雅克比，push到obv_jacobian中。  
*solveAndUpdate()*：执行卡尔曼滤波的更新流程，计算卡尔曼因子k和后验误差状态，并更新系统（名义）状态和系统协方差。  
*updateWithOdom()*：输入odom观测信息，首先通过getDelayUpdateInfo得到延迟更新信息，然后计算观测残差和观测雅克比并调用addResidualJacobian()添加到obv_res和obv_jacobian中，设置本次观测的噪声矩阵，最后调用solveAndUpdate()实现kf更新。  
*updateWithZUPT()*：输入imu观测，构建零速更新的残差项和雅克比，从而实现零速更新。  

## 系统Pipeline——KfInterface类
**重要成员变量：**  
*thrd_hdl*：C11线程句柄。  
*meas_queue*：缓存队列，存储接收到的观测数据。  
*kf_coordinator*：封装了eskf相关操作。  
*state_initializer*：封装了kf初始化相关操作。  
*static_check*：零速检测器，目前实现了基于imu滑窗的静止判定，后续会被vins零速检测替代。  
*pub_xxx / sub_xxx*：ros发布和订阅句柄。  
**重要成员方法：**  
*receiveImuTopic()*：imu话题订阅回调函数，包装数据push到队列，通过条件变量唤醒处理线程。  
*receiveOdomTopic()*：odom话题订阅回调函数，包装数据push到队列，通过条件变量唤醒处理线程。  
*publishxxx()*：通过ros发布相关处理结果。  
*processMeasurements()*：作为处理线程入口函数，当被唤醒时，处理观测数据(while遍历处理队列里的所有数据)，具体逻辑:

1. 判定是否kf完成初始化，若没有初始化则调用state_initializer.initState()以及kf_coordiantor_.init()方法完成初始化。
2. 若已完成初始化，如果当前测量数据是imu，则调用kf_coordiantor.imuStatePropagate()递推状态和协方差，并调用static_check.inputImu()检测是否检测到静止，若检测到静止则调用kf_coordiantor.updateWithZUPT()进行零速更新；若是odom或gps数据，调用相关update函数实现kf更新。
3. 通过ros广播相关处理结果。

# 外参离线标定工具
kf-fusion融合外部里程计时，考虑了imu坐标系到里程计机体系之间的相对位姿即外参，但是经过实际测试发现在线标定效果较差，原因是目前的观测模型无法使外参变得可观，因此kf-fusion暂时取消在线估计外参，单独开发了一个基于手眼标定法的简易外参离线标定工具，用于标定两个相互固定且独立的里程计之间单独外参。  
## 使用
1. 在config/config.yaml中修改两个里程计的话题名，目前默认为动捕里程计话题名和vins里程计话题名：  
   ```plain
   odom_topic: "/vins_fusion/odometry"
   motion_capture_topic: "/motion_capture/motion_capture_odom"
   ```
2. 依次启动两个里程计后，再启动标定工具：  
   ```plain
   #启动vins
   sh shfiles/rspx4_xp.sh
   #启动动捕
   roslaunch motion_capture motion_capture.launch
   #启动外参标定工具
   roslaunch kf_fusion ext_calib.launch
   ```
3. 启动外参标定工具后注意终端打印的日志，出现提示“Calibration start, please move the drone fully.”后即可移动机体，保证六自由度的充分运动，程序会自动截取运动充分的数据用于结算外参。  
4. 终端会实时打印有效数据的数量，当有效数量大于50时，若持续2秒没有检测到有效数据，则会停止采集数据，进行外参解算。为了保证求解精度，建议持续运动保证有效数据数量在100以上。外参求解结果会打印在终端：  
   ```plain
   [ WARN] [1765373385.708512653]: Collecting data finished, total size is 411.
   [ WARN] [1765373385.710690551]: Start solve external pose.
   [ WARN] [1765373385.753432781]: Solve external rotation successfully!
   External rotation calib result is:
     0.996615 -0.0312618  0.0760409
    0.0341498   0.998732 -0.0369798
   -0.0747885  0.0394514   0.996419
   [ WARN] [1765373385.755121709]: Solve external position successfully!.
   External position calib result is:
   -0.0491892
     0.041708
    0.0242918
   ```

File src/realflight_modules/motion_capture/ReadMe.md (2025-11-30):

# 功能
VINS-Fusion后端输出的里程计的格式是nav_msgs::Odometry，目前使用到的数据有：

位置p的xyz，姿态四元数 xyzw，速度v的xyz，角速度w的xyz

动捕输出的三个话题（uav0是动捕系统软件中定义的刚体名称）

| topic | 类型 | 成员 |
| --- | --- | --- |
| /vrpn_client_node/uav0/pose | geometry_msgs/PoseStamped | position->x,y,z<br/>orientation->x,y,z,w |
| /vrpn_client_node/uav0/twist | geometry_msgs/TwistStamped | linnear->x,y,z<br/>angel->x,y,x |
| /vrpn_client_node/uav0/accel | geometry_msgs/TwistStamped | linnear->x,y,z<br/>angel->x,y,x |

所以需要将动捕输出的3个Topic整合为一个动捕里程计话题进行集中输出，本ROS包通过固定Pose的数据和时间，将Twist和Accel数据进行线性插值计算出和Pose时间戳对齐的数据，最后打包整合发布在/motion_capture/motion_capture_odom

# 使用
1. 使用动捕系统软件创建刚体，并且打开VRPN输出流（打开速度、加速度输出）
2. 运行脚本

```plain
chmod +x ./shfile/motion_capture_receive_publish.sh
./shfile/motion_capture_receive_publish.sh
```

3. 即可订阅动捕转换的里程计数据，Topic：/motion_capture/motion_capture_odom，类型：nav_msgs/Odometry

# 参数配置
在ROS的config文件夹下可以配置

```yaml
动捕的三个话题的topic
motion_capture_pose_topic: "/vrpn_client_node/uav0/pose"
motion_capture_twist_topic: "/vrpn_client_node/uav0/twist"
motion_capture_accel_topic: "/vrpn_client_node/uav0/accel"
```

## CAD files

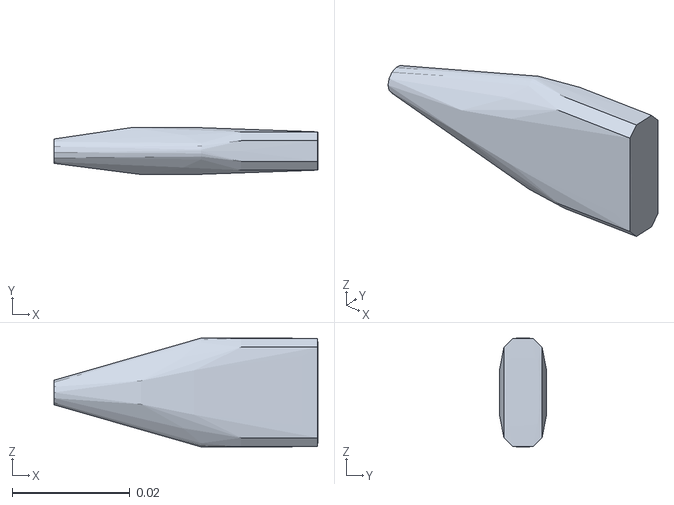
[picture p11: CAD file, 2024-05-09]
src/realflight_modules/realsense-ros/realsense2_description/meshes/plug_collision.stl
0.0448 x 0.008 x 0.0185

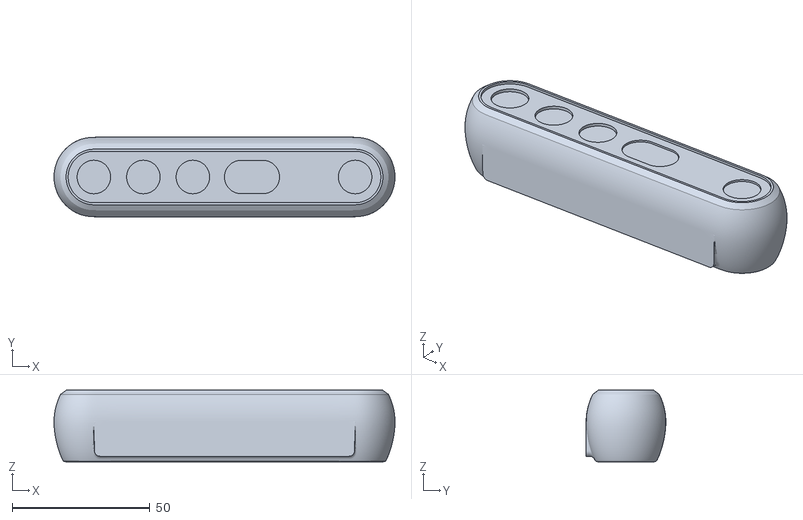
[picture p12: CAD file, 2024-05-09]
src/realflight_modules/realsense-ros/realsense2_description/meshes/d455.stl
124.0 x 29.0 x 26.0

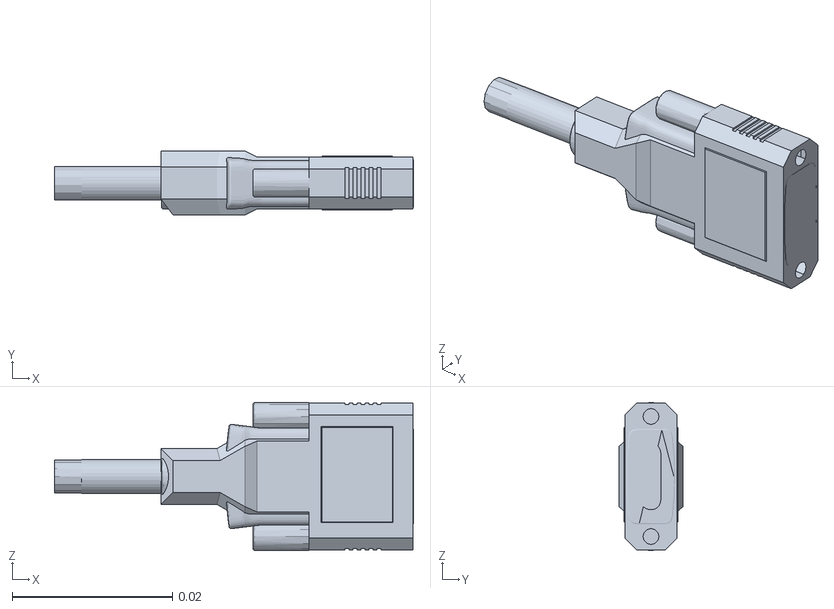
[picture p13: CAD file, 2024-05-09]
src/realflight_modules/realsense-ros/realsense2_description/meshes/plug.stl
0.0448 x 0.008 x 0.0185

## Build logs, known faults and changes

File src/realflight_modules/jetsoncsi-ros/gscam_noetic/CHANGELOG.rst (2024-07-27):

^^^^^^^^^^^^^^^^^^^^^^^^^^^
Changelog for package gscam
^^^^^^^^^^^^^^^^^^^^^^^^^^^

1.0.1 (2018-09-06)
------------------
* Merge pull request `#52 <https://github.com/ros-drivers/gscam/issues/52>`_ from k-okada/add_travis
  update travis.yml
* Update README.md
  gscam -> GSCam
* update travis.yml
* Merge pull request `#40 <https://github.com/ros-drivers/gscam/issues/40>`_ from ros-drivers/mikaelarguedas-patch-1
  update to use non deprecated pluginlib macro
* update to use non deprecated pluginlib macro
* Contributors: Kei Okada, Mikael Arguedas

1.0.0 (2017-06-13)
------------------
* Gstreamer 1 0 support (`#36 <https://github.com/ros-drivers/gscam/issues/36>`_ )
  * delete unused manifest.xml, rosdep.yaml
  * use libgstreamer1.0 for lunar
  * Fixing preproc switches so that the 1.0 branch still builds against 0.1 without the switch flags
  * Preliminary GStreamer-1.0 support see README for more info
* Contributors: Jonathan Bohren, Kei Okada

0.2.0 (2017-06-13)
------------------
* add ROS Orphaned Package Maintainers to maintainer tag (`#35 <https://github.com/ros-drivers/gscam/issues/35>`_ )
* gscam_nodelet.h: include scoped_ptr.hpp to compile with boost 1.57
  When compiling gscam with the currently latest boost version 1.57,
  it fails with:
  In file included from [...]/src/gscam_nodelet.cpp:5:0:
  [...]/include/gscam/gscam_nodelet.h:20:12: error: 'scoped_ptr' in namespace 'boost' does not name a template type
  boost::scoped_ptr<GSCam> gscam_driver\_;
  ^
  [...]/include/gscam/gscam_nodelet.h:21:12: error: 'scoped_ptr' in namespace 'boost' does not name a template type
  boost::scoped_ptr<boost::thread> stream_thread\_;
  ^
  It seems that the dependencies of boost/thread.hpp have changed
  and boost/scoped_ptr.hpp is not included anymore with
  boost/thread.hpp. Hence, the scoped_ptr is not defined in the
  gscam_nodelet header. After scanning quickly through the release
  notes of version 1.57, the boost bug tracker and a few changesets,
  I could not find not a hint what has changed in the thread library
  that gscam must include scoped_ptr itself.
  This commit simply addresses the compiler error by explicitly
  adding boost's scoped_ptr header in the gscam_nodelet header.
  As this commit also compiles with boost version 1.56, the commit
  is not expected to cause any problems with other build
  configurations.
  Signed-off-by: Lukas Bulwahn <lukas.bulwahn@oss.bmw-carit.de>
* Remove dependency on opencv2 to fix under indigo
  Packages can no longer depend on opencv2 as of indigo.
  I've updated the package to depend instead on cv_bridge as suggested by http://wiki.ros.org/indigo/Migration#OpenCV.
* Install the parameters file refered to in v4l.launch
* Update package.xml
* Examples: Added example for OSX (`#15 <https://github.com/ros-drivers/gscam/issues/15>`_)
  Add a simple launch configuration for OSX. The camera can be selected by
  changing the default="0" to the appropriate integer.
* Adding libraries to gscam target
  Fixes `#13 <https://github.com/ros-drivers/gscam/issues/13>`_, now builds on stricter linkers
* adding proper depends to catkin package call
* Update minoru.launch
* Contributors: CHILI Demo Corner, Jonathan Bohren, Kei Okada, Kenn Sebesta, Lukas Bulwahn, Russell Toris, Lukas Bulwahn

0.1.3 (2013-12-19)
------------------
* Removed special characters from changelog.

0.1.2 (2013-12-19)
------------------
* Added install targets for headers
* Adding note on blackmagic decklink cards
* Make sure nodelets are usable
* Add jpeg direct publishing without decoding
* Added system to use GST timestamps
* Valid test file for jpeg-based publisher
* Prepared for jpeg-only subscription
* Install some launch files + added nodelet pipeline demo
* Added missing bits to install the nodelet
* Support for gray (mono8) cameras.
* Remove unused ``bpp_`` member.
* Expose default settings for ``image_encodings`` to the ros master.
* Add in support for mono cameras.
* Contributors: Cedric Pradalier, Holger Rapp, Jonathan Bohren, Russell Toris, Severin Lemaignan

0.1.1 (2013-05-30)
------------------
* adding missing nodelet dep
* Contributors: Jonathan Bohren

0.1.0 (2013-05-28)
------------------
* adding maintainer/authors
* making node name backwards compatible
* re-adding package.xml
* more info spam
* removing old camera parameters file
* updating gscam to use ``camera_info_manager``
* Fixing nodelet, adding example
* Making gscam a node and nodeelt
* adding a note on the videofile player and wrapping readme
* adding option to reopen a stream on EOF and adding a videofile example
* Hybrid catkin-rosbuild buildsystem
* adding minoru example
* putting example nodes into namespaces, adding correct error check in gscam source, making tf frame publishing optional
* rst->md
* making gscam conform to standard ``camera_drivers`` ROS API, note, still need to add polled mode
* fixes for decklink capture, adding another example
* can't have manifest.xml and package.xml in same directory
* removing unneeded find-pkgs
* building in catkin ws
* hybrid rosbuild/catkin buildsystem
* Adding changes that were made to the distribution branch that
  should have gone into the exerpeimental branch in r2862.
  Added a bunch of enhancements and fixed bugs involving data
  missing fromthe image message headers.
  Index: src/gscam.cpp
  ===================================================================
  Added ``camera_name`` and ``camera_parameters_file`` globals for camera
  info.
  Moved ros init to the top of the main function.
  Gets the gstreamer configuration either from environment variable
  ``GSCAM_CONFIG`` or ROS param ``~/gscam_config``.
  Gets the camera calibration parameters from the file located at ROS
  param ``~/camera_parameters_file``, will look at
  "../camera_settings.txt" by default.
  A bunch of re-indenting for consistency.
  Updated a lot of error fprintfs to ``ROS_ERROR`` calls.
  Gets the TF ``frame_id`` from the ROS param ``~/frame_id``, can be over-
  written by camera parameters.
  Now sets the appropriate ROS timestap in the image message header.
  Now sets the appropriate TF frame in the image message header.
  Added more detailed info/error/warn messages.
  Modified the warning / segfault avoidance added to experimental in
  r2756. Instead of skipping the frame, it just copies only the
  amount of data that it was received, and reports the warning each
  time, instead of just once. In a large scale system with lots of
  messages, a single warning might easily get lost in the noise.
  Index: examples/webcam_parameters.txt
  ===================================================================
  Added example camera parameters (uncalibrated) for a laptop webcam.
  Index: examples/webcam.launch
  ===================================================================
  Added a launchfile that makes use of the new rosparam options and
  TF frame.
* avoid segfault when buffer size is too small
* ROSProcessingjs clean-up
* makefile so rosmake is more reliable
* gscam build tweak for oneiric
* fixes for Natty build per Willow request
* stop node on EOS
* File support courtesy of John Hoare of the University of Tennesse at Knoxville
* more conservative license policy
* fps workaround
* ding gscam
* back to before
* two publishers
* Lots of changes.  AR Alpha now expects files in the bin directory, to facilitate roslaunch.  Gscam must be started from the bin directory, or, again, using roslaunch.  The localizer code now works correctly and has been tested on a Create, but has problems cause by AR alpha's processing delays.
* Bugfix: supply default camera parameters when real ones are unavailable.
* Fully-functional calibration file writing.
* Partial changes for file-writing gscam.
* Gscam now fits into an image processing pipeline with rectified images.  TODO: Save camera configuration info.
* Handles built for camera info services, but no testing.
* Changed the name of the GStreamer camera package.  probe will henceforth be known as gscam.
* Contributors: Jonathan Bohren, chriscrick, evan.exe@gmail.com, nevernim@gmail.com, trevorjay

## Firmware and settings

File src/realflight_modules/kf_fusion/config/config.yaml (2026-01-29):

#ros topic
imu_topic: "/imu_filter/data" #/imu_filter/data /mavros/imu/data_raw
odom_topic: "/vins_fusion/odometry"
motion_capture_topic: "/motion_capture/motion_capture_odom"
vins_valid_topic: "/vins_fusion/vins_fail"

#imu noise parameter
accel_noise_std: 0.1
gyro_noise_std: 0.02
accel_walk_std: 1e-3
gyro_walk_std: 1e-4

# motion capture
use_motion_capture: true

# bias relevant
enable_merge_vins_bias: true #融合vins零偏
bias_accel_init: [-0.14, 0.038, 0.167]

#init state_cov
imu_ori_init_cov: 4e-5
imu_yaw_init_cov: 1e-5
imu_posi_init_cov: 1e-5
imu_vel_init_cov: 0.1 #0.09
gyro_bias_init_cov: 1e-7
acc_bias_init_cov: 0.1 #1e-2
ext_ori_init_cov: 1e-6
ext_posi_init_cov: 1e-4

#obv odom cov
obv_odom_rot_cov: [0.001, 0.001, 0.005] #[0.02, 0.02, 0.05]
obv_odom_posi_cov: [0.005, 0.005, 0.01] #[0.05, 0.05, 0.1]
obv_odom_vel_cov: [0.001, 0.001, 0.002] #[0.01, 0.01, 0.02]
obv_vins_bias_cov: [0.001, 0.001, 0.002]

#motion capture cov
obv_mc_rot_cov: [0.0005, 0.0005, 0.0005] #[0.02, 0.02, 0.05]
obv_mc_posi_cov: [0.001, 0.001, 0.001] #[0.05, 0.05, 0.1]
obv_mc_vel_cov: [0.001, 0.001, 0.001] #[0.01, 0.01, 0.02]

#zupt cov
obv_zupt_gyro_cov: [0.0001, 0.0001, 0.0005]
obv_zupt_accel_cov: [0.0001, 0.0001, 0.0005]
obv_zupt_vel_cov: [0.0001, 0.0001, 0.0005]

#initializer
static_check_dura_s: 5.0
thresh_gyro_avg: 0.01
thresh_accel_avg: 0.2 
thresh_gyro_var: 0.002
thresh_accel_var: 0.1

#odom external param
T_imu_body:
  - [1.0, 0.0, 0.0, 0.0]
  - [0.0, 1.0, 0.0, 0.0]
  - [0.0, 0.0, 1.0, 0.0]
  - [0.0, 0.0, 0.0, 1.0]

#motion external param
T_imu_mbody:
  - [1.0, 0.0, 0.0, -0.055]
  - [0.0, 1.0, 0.0, 0.055]
  - [0.0, 0.0, 1.0, 0.025]
  - [0.0, 0.0, 0.0, 1.0]

# enable estimation of ext-param
estimate_ext_rot: false
estimate_ext_tvec: false

#kf_coordinator
imu_que_dura_length: 1  #unit:s

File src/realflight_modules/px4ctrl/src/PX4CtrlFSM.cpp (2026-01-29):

#include "PX4CtrlFSM.h"
#include <uav_utils/converters.h>

using namespace std;
using namespace uav_utils;

PX4CtrlFSM::PX4CtrlFSM(Parameter_t &param_, LinearControl &controller_)
    : param(param_),
      controller(controller_) /*, thrust_curve(thrust_curve_)*/
{
    state = MANUAL_CTRL;
    hover_pose.setZero();
    imu_acc_lpf.setZero();
    flag_init_imu_acc_lpf = false;
}

/*
        Finite State Machine

          system start
                |
                |
                v
    ----- > MANUAL_CTRL <-----------------
    |         ^   |    \                 |
    |         |   |     \                |
    |         |   |      > AUTO_TAKEOFF  |
    |         |   |        /             |
    |         |   |       /              |
    |         |   |      /               |
    |         |   v     /                |
    |       AUTO_HOVER <                 |
    |         ^   |  \  \                |
    |         |   |   \  \               |
    |         |	  |    > AUTO_LAND -------
    |         |   |
    |         |   v
    -------- CMD_CTRL

*/

void PX4CtrlFSM::process() {
    ros::Time now_time = ros::Time::now();
    Controller_Output_t u;
    Desired_State_t des(odom_data);
    bool rotor_low_speed_during_land = false;

    // STEP1: state machine runs
    switch (state) {
        case MANUAL_CTRL: {
            if (kf_fusion_fail) {
                ROS_ERROR("[px4ctrl] kf fusion is failed, please take land manually!");
                break;
            }
            if (rc_data.enter_hover_mode)  // Try to jump to AUTO_HOVER
            {
                if (!odom_is_received(now_time)) {
                    ROS_ERROR("[px4ctrl] Reject AUTO_HOVER(L2). No odom!");
                    break;
                }
                if (cmd_is_received(now_time)) {
                    ROS_ERROR(
                        "[px4ctrl] Reject AUTO_HOVER(L2). You are sending commands before toggling "
                        "into AUTO_HOVER, which is not allowed. Stop sending commands now!");
                    break;
                }
                if (odom_data.v.norm() > 3.0) {
                    ROS_ERROR(
                        "[px4ctrl] Reject AUTO_HOVER(L2). Odom_Vel=%fm/s, which seems that the "
                        "locolization module goes wrong!",
                        odom_data.v.norm());
                    break;
                }

                state = AUTO_HOVER;
                controller.resetThrustMapping(bat_data);
                set_hov_with_odom();
                toggle_offboard_mode(true);

                ROS_INFO("\033[32m[px4ctrl] MANUAL_CTRL(L1) --> AUTO_HOVER(L2)\033[32m");
            } else if (
                param.takeoff_land.enable && takeoff_land_data.triggered &&
                takeoff_land_data.takeoff_land_cmd ==
                    quadrotor_msgs::TakeoffLand::TAKEOFF)  // Try to jump to AUTO_TAKEOFF
            {
                if (!odom_is_received(now_time)) {
                    ROS_ERROR("[px4ctrl] Reject AUTO_TAKEOFF. No odom!");
                    break;
                }
                if (cmd_is_received(now_time)) {
                    ROS_ERROR(
                        "[px4ctrl] Reject AUTO_TAKEOFF. You are sending commands before toggling "
                        "into AUTO_TAKEOFF, which is not allowed. Stop sending commands now!");
                    break;
                }
                if (odom_data.v.norm() > 0.1) {
                    ROS_ERROR(
                        "[px4ctrl] Reject AUTO_TAKEOFF. Odom_Vel=%fm/s, non-static takeoff is not "
                        "allowed!",
                        odom_data.v.norm());
                    break;
                }
                if (!get_landed()) {
                    ROS_ERROR(
                        "[px4ctrl] Reject AUTO_TAKEOFF. land detector says that the drone is not "
                        "landed now!");
                    break;
                }
                if (rc_is_received(now_time)) {
                    if (!rc_data.is_hover_mode || !rc_data.is_command_mode ||
                        !rc_data.check_centered()) {
                        ROS_ERROR(
                            "[px4ctrl] Reject AUTO_TAKEOFF. If you have your RC connected, keep "
                            "its switches at \"auto hover\" and \"command control\" states, and "
                            "all sticks at the center, then takeoff again.");
                        while (ros::ok()) {
                            ros::Duration(0.01).sleep();
                            ros::spinOnce();
                            if (rc_data.is_hover_mode && rc_data.is_command_mode &&
                                rc_data.check_centered()) {
                                ROS_INFO("\033[32m[px4ctrl] OK, you can takeoff again.\033[32m");
                                break;
                            }
                        }
                        break;
                    }
                }

                state = AUTO_TAKEOFF;

                if (!bat_is_received(now_time)) {
                    ROS_ERROR("[px4ctrl] Don't receive bat_data.");
                    while (!bat_is_received(now_time) && ros::ok()) {
                        ros::Duration(0.01).sleep();
                        ros::spinOnce();
                    }
                }
                controller.resetThrustMapping(bat_data);

                set_start_pose_for_takeoff_land(odom_data);
                toggle_offboard_mode(true);  // toggle on offboard before arm
                for (int i = 0; i < 10 && ros::ok();
                     ++i)  // wait for 0.1 seconds to allow mode change by FMU // mark
                {
                    ros::Duration(0.01).sleep();
                    ros::spinOnce();
                }
                if (param.takeoff_land.enable_auto_arm) {
                    toggle_arm_disarm(true);
                }
                takeoff_land.toggle_takeoff_land_time = now_time;

                ROS_INFO("\033[32m[px4ctrl] MANUAL_CTRL(L1) --> AUTO_TAKEOFF\033[32m");
            }

            if (rc_data.toggle_reboot)  // Try to reboot. EKF2 based PX4 FCU requires reboot when
                                        // its state estimator goes wrong.
            {
                if (state_data.current_state.armed) {
                    ROS_ERROR("[px4ctrl] Reject reboot! Disarm the drone first!");
                    break;
                }
                reboot_FCU();
            }

            break;
        }

        case AUTO_HOVER: {
            if (!rc_data.is_hover_mode || !odom_is_received(now_time) || kf_fusion_fail) {
                state = MANUAL_CTRL;
                toggle_offboard_mode(false);
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

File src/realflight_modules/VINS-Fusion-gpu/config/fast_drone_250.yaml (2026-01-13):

%YAML:1.0

#common parameters
#support: 1 imu 1 cam; 1 imu 2 cam: 2 cam; 
imu: 1         
num_of_cam: 2


imu_topic: "/imu_filter/data"
image0_topic: "/camera/infra1/image_rect_raw"
image1_topic: "/camera/infra2/image_rect_raw"




output_path: "/root/Fast-Drone-XI35/vins_output"


cam0_calib: "left.yaml"
cam1_calib: "right.yaml"
image_width: 640
image_height: 480
   

# Extrinsic parameter between IMU and Camera.
estimate_extrinsic: 1   # 0  Have an accurate extrinsic parameters. We will trust the following imu^R_cam, imu^T_cam, don't change it.
                        # 1  Have an initial guess about extrinsic parameters. We will optimize around your initial guess.


#body_T_cam0: !!opencv-matrix
#   rows: 4
#   cols: 4
#   dt: d
#   data: [ 0., 0.,
#       1.0, 8.6e-02,
#       -1.0, 0.,
#       0., 7.5e-03,
#       0., -1.0,
#       0., 2.8e-02, 0., 0., 0., 1. ]
#body_T_cam1: !!opencv-matrix
#   rows: 4
#   cols: 4
#   dt: d
#   data: [ 0., 0.,
#       1.0, 8.6e-02,
#       -1.0, 0.,
#       0., -4.25e-02,
#       0., -1.0,
#       0., 2.8e-02, 0., 0., 0., 1. ]

body_T_cam0: !!opencv-matrix
   rows: 4
   cols: 4
   dt: d
   data: [ -0.023812, -0.0292592, 1.00098, 0.0398414,
           -0.999804, -0.00650283, -0.0235935, 0.0041051,
           -0.00856173, -1.00134, 0.0287238, 0.0254451,
            0., 0., 0., 1. ]
body_T_cam1: !!opencv-matrix
   rows: 4
   cols: 4
   dt: d
   data: [  -0.0190521, -0.0297924, 1.00187, 0.0389944,
            -1.00051, 0.00690096, 0.018821, -0.0440594,
            -0.00859325, -1.0013, 0.0299389, 0.0251162,
            0., 0., 0., 1. ]

#Multiple thread support
multiple_thread: 1
use_gpu: 1
use_gpu_acc_flow: 1

#feature traker paprameters
max_cnt: 150            # max feature number in feature tracking
min_dist: 30            # min distance between two features 30
freq: 10                # frequence (Hz) of publish tracking result. At least 10Hz for good estimation. If set 0, the frequence will be same as raw image 
F_threshold: 1.0        # ransac threshold (pixel)
show_track: 1           # publish tracking image as topic
flow_back: 1            # perform forward and backward optical flow to improve feature tracking accuracy

#optimization parameters
max_solver_time: 0.04  # max solver itration time (ms), to guarantee real time
max_num_iterations: 8   # max solver itrations, to guarantee real time
keyframe_parallax: 10.0 # keyframe selection threshold (pixel)

#imu parameters       The more accurate parameters you provide, the better performance
acc_n: 0.1          # accelerometer measurement noise standard deviation. #0.2   0.04
gyr_n: 0.01         # gyroscope measurement noise standard deviation.     #0.05  0.004
acc_w: 0.001         # accelerometer bias random work noise standard deviation.  #0.002
gyr_w: 0.0001       # gyroscope bias random work noise standard deviation.     #4.0e-5
g_norm: 9.8066         # gravity magnitude

#unsynchronization parameters
estimate_td: 1                      # online estimate time offset between camera and imu
#td: -0.003116                            # initial value of time offset. unit: s. readed image clock + td = real image clock (IMU clock)
td: -0.001                           # -0.001 initial value of time offset. unit: s. readed image clock + td = real image clock (IMU clock)

#loop closure parameters
load_previous_pose_graph: 0        # load and reuse previous pose graph; load from 'pose_graph_save_path'
pose_graph_save_path: "/home/orin02/savedfiles/output/pose_graph/" # save and load path
save_image: 1                   # save image in pose graph for visualization prupose; you can close this function by setting 0 

odometry_type: 0 #0为原始里程计，1为加了偏置后的里程计
drone_id: 1
single_offset: 2.0

enable_pub_imu_path: 1 #发布里程计轨迹

enable_imu_odom_smooth: 1   #平滑imu里程计
velocity_limit: 1.5

enable_ex_prior: 0  #对外参施加先验
ex_prior_sqrt_info: 10000  #外参先验因子权重 5000

use_external_front_end: 1 #0：前端使用自带的光流跟踪，1：使用外部特征跟踪器

record_csv: 0 #记录滑窗优化最新帧的时间戳、滑窗内可用的特征点数目、xyz、td
csv_file_path: "/home/nx05/csv/vins_backend/xp_opticalflow_retrack.csv" #sp_opticalflow.csv, sp_lg_version.csv, original_version.csv, xp_opticalflow.csv
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

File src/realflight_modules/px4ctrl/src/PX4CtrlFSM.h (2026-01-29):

#ifndef __PX4CTRLFSM_H
#define __PX4CTRLFSM_H

#include "input.h"
#include <geometry_msgs/PoseStamped.h>
#include <mavros_msgs/CommandBool.h>
#include <mavros_msgs/CommandLong.h>
#include <mavros_msgs/SetMode.h>
#include <nav_msgs/Odometry.h>
#include <ros/assert.h>
#include <ros/ros.h>
#include <std_msgs/Bool.h>
// #include "ThrustCurve.h"
#include "controller.h"

struct AutoTakeoffLand_t {
    bool landed{true};
    ros::Time toggle_takeoff_land_time;
    std::pair<bool, ros::Time> delay_trigger{std::pair<bool, ros::Time>(false, ros::Time(0))};
    Eigen::Vector4d start_pose;

    static constexpr double MOTORS_SPEEDUP_TIME =
        3.0;  // motors idle running for 3 seconds before takeoff
    static constexpr double TAKEOFF_SPEEDUP_TIME =
        0.1;  // Time to speed up during takeoff font stage
    static constexpr double DELAY_TRIGGER_TIME =
        2.0;  // Time to be delayed when reach at target height
};

class PX4CtrlFSM {
  public:
    Parameter_t &param;

    RC_Data_t rc_data;
    State_Data_t state_data;
    ExtendedState_Data_t extended_state_data;
    Odom_Data_t odom_data;
    Imu_Data_t imu_data;
    Command_Data_t cmd_data;
    Battery_Data_t bat_data;
    Takeoff_Land_Data_t takeoff_land_data;

    Eigen::Vector3d imu_acc_lpf;  // output of LPF
    bool flag_init_imu_acc_lpf;
    double a_lpf;
    double b_lpf;

    LinearControl &controller;

    ros::Publisher traj_start_trigger_pub;
    ros::Publisher ctrl_FCU_pub;
    ros::Publisher debug_pub;  // debug
    ros::ServiceClient set_FCU_mode_srv;
    ros::ServiceClient arming_client_srv;
    ros::ServiceClient reboot_FCU_srv;
    ros::ServiceClient set_bat_freq;

    quadrotor_msgs::Px4ctrlDebug debug_msg;  // debug

    Eigen::Vector4d hover_pose;
    ros::Time last_set_hover_pose_time;

    enum State_t {
        MANUAL_CTRL = 1,  // px4ctrl is deactived. FCU is controled by the remote controller only
        AUTO_HOVER,  // px4ctrl is actived, it will keep the drone hover from odom measurments while
                     // waiting for commands from PositionCommand topic.
        CMD_CTRL,    // px4ctrl is actived, and controling the drone.
        AUTO_TAKEOFF,
        AUTO_LAND
    };

    PX4CtrlFSM(Parameter_t &, LinearControl &);
    void process();
    void process_new();
    bool rc_is_received(const ros::Time &now_time);
    bool cmd_is_received(const ros::Time &now_time);
    bool odom_is_received(const ros::Time &now_time);
    bool imu_is_received(const ros::Time &now_time);
    bool bat_is_received(const ros::Time &now_time);
    bool recv_new_odom();
    State_t get_state() { return state; }
    bool get_landed() { return takeoff_land.landed; }

    void LPF_imu_a(Eigen::Vector3d &imu_data_acc);

    // add by bk
    bool emergency_hover = false;
    void emergency_callback(const std_msgs::BoolConstPtr &msg) {
        // if(msg->data == true)
        // 	emergency_hover = true;
    }

    bool search_hover = false;
    void search_hover_callback(const std_msgs::BoolConstPtr &msg) { search_hover = msg->data; }

    bool kf_fusion_fail = false;
    void kf_fail_callback(const std_msgs::BoolConstPtr &msg) {
        if (msg->data == true) kf_fusion_fail = true;
    }

  private:
    State_t state;  // Should only be changed in PX4CtrlFSM::process() function!
    AutoTakeoffLand_t takeoff_land;

    // ---- control related ----
    Desired_State_t get_hover_des();
    Desired_State_t get_cmd_des();

    // ---- auto takeoff/land ----
    void motors_idling(const Imu_Data_t &imu, Controller_Output_t &u);
    void land_detector(
        const State_t state, const Desired_State_t &des,
        const Odom_Data_t &odom);  // Detect landing
    void set_start_pose_for_takeoff_land(const Odom_Data_t &odom);
    Desired_State_t get_rotor_speed_up_des(const ros::Time now);
    Desired_State_t get_takeoff_land_des(const double speed);

    // ---- tools ----
    void set_hov_with_odom();
    void set_hov_with_rc();

    bool toggle_offboard_mode(bool on_off);  // It will only try to toggle once, so not blocked.
    bool toggle_arm_disarm(bool arm);        // It will only try to toggle once, so not blocked.
    void reboot_FCU();

    void publish_bodyrate_ctrl(const Controller_Output_t &u, const ros::Time &stamp);
    void publish_attitude_ctrl(const Controller_Output_t &u, const ros::Time &stamp);
    void publish_trigger(const nav_msgs::Odometry &odom_msg);
};

#endif

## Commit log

2024-05-28 1) add launch for exp; 2) add launch-prefix for gbd 3) change wallfollower CMAKE_CXX_FLAG_RELEASE -O3 to -O0 4) remove some debug print in wall_follower.cpp
2024-07-26 add two features: - det-reg-pnp -jetsoncsi-ros
2024-07-29 add states print feature
2024-07-29 1) fix target height bug by setting target.z = current_position.z 2) fix param name bug; 3) add some position and distance print.
2024-07-30 modify jetson_csi_cam.launch
2024-08-01 1) fix wps_[wp_id_] out of bound accessing; 2) fix no resetting has_slow_down_req_ to false 3) using the first position in the moment of switching to slowdown as current_Target intead of using curren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
2024-08-03 1) add slow_down_height_, my_target_hover_height_ and make publish_target_threshold_ be a param; 2) current_Target is assigned by wps_[wp_id_] only after checking has_found_my_target_ and has_slow_do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
2024-08-04 update vins-odometry offset
2024-08-06 make vins track img to be a topic rather than a opencv UI
2024-09-12 make jetsoncsi suit for multi-cam
2024-09-18 fix a bug about param_.gra
    [PX4CtrlFSM.cpp]
2024-10-24 Estimate thrust model using velocity feed back
2024-10-24 add LPF for imu_a_z that is input of estimateThrustModel
2024-11-27 add track cnt show
2024-12-01 fix prewarm bug for xfeat, add DetectHDUseXfeat
    [fast_drone_250.yaml]
2024-12-02 fix thrust_calibrate.py bug; change mass
2024-12-02 change /mavros/battery 0.5hz to 10hz
2024-12-02 1) using batttary volt and mass to estimate takeoff hover percentage; 2) add acurate thr model using bat volt but not good so not using yet; 3) fix bat volt lpf init problem
    [PX4CtrlFSM.cpp, PX4CtrlFSM.h]
2024-12-06 tune the pid param to responed faster
2024-12-17 try to solve the traj-spike, smooth the imu-odom path
2025-05-20 make bat msg have higher freq (10HZ)
2025-05-20 start stage collabration v1
2025-05-21 add terminator config file for two drone start stage collabration, using lcm_node in lab WIFI.
2025-09-01 Fix a bug in PX4CtrlFSM.cpp
    controller.resetThrustMapping(bat_data) Only suit for 6s bat, not 4s yet. backroll to controller.resetThrustMapping() for 4s.
    [PX4CtrlFSM.cpp]
2025-11-03 NEW: Add IMU filter ROS node for VINS
2025-11-30 NEW: convert motion capture Topic to nav_msgs/Odometry
2025-12-10 NEW: add support for external calibration for kf_fusion.Please refer to the README for details.
2025-12-10 NEW: add README for external calibration.
2026-01-05 NEW: 1.add a optical flow prediction algorithm. 2.perform secondary verification using xfeat descriptor for optical flow. 3.optimize the performance of retrack.
2026-01-07 FIX: fix some bugs in PX4ctrl
    1. 适配4S电池的两端油门-电压映射
    2. PX4 Ctrl 控制结构和参数调整
    3. 输出推力进行倾斜姿态补偿
    4. 一些小bug
    5. 代码格式优化
    6. 容器初始化的环境变量路径错误
    7. rosservice call /mavros/set_message_interval 147 10.0 ，对电池mavros信息升频放在px4ctrl节点初始化
    8. 修改新机型的外参、重量
    [PX4CtrlFSM.cpp, PX4CtrlFSM.h, ctrl_param_fpv.yaml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]
2026-01-29 NEW: 1.add health monitor for kf_fusion 2.add kf_fusion.sh 3.forced manual control mode when kf fusion failed
    [PX4CtrlFSM.cpp, PX4CtrlFSM.h, config.yaml]
2026-02-03 Docker configuration on an x86 host (#5)
    * NEW: Add PC docker files
    * NEW: Add Docker pc README
    * FIX: CUDA_ARCH_BIN cannot be obtained during the container build process.
    * NEW: Add nvidia jetson Docker build ReadME.md
    ---------
